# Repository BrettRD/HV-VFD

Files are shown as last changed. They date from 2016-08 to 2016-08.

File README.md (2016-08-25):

# HV-VFD
Staging point for design of a motor controller to suit electric vehicles.

This project is intended as a rework of https://github.com/vedderb/bldc-hardware/ to suit systems operating beyond the power ratings of the VESC 4.x.

## Major design goals:
* 400V tolerant system.
* 400A overcurrent survivability.
* FET desaturation detection.
* Maximise forward compatibility with existing development efforts.
* Traction power and logic level isolation
* Flexibility for alternate applications.

### FETs
This design will be based on the SEMiX402GB066HDs by Semikron, but will hopefully support everything in their SEMiX_2s pack.  
This sets the price point fairly high, but will require a rock solid gate driver design.  
I expect this project to branch for different IGBT sizes.  

### FET Drivers
The FET drivers need an estimated 6A to reach 400A IGBTs  
Currently designing around the 1EDI60H12AH by infineon

### Desaturation detector / phase shunt monitor
Depending on the required bandwidth for the phase shunts, a PWM based isolation amp like the IRF2277 might suffice.  
This design will also include a Vsat monitor on all fets, but probably just a fast comparator.  
Current best practice for IGBTs seems to be soft shutdown at some Vsat threshold, for MOSFETs Vsat only helps with estimating the total instantaneous heat power per junction.  

### Architecture
External logic lines will not be linked to traction power in any way.  
High voltage gate drivers are isolated by default, and are mostly available as single-gate drivers.  
Gate handling logic will be on the logic-side, so desat detect and shunt monitoring will all require isolation.  
Given the FET package and the current, the shunts will almost certainly be off-board which makes Hall effect sensors less of a design change.

## Considerations:
### Phase or Rail shunts:  
Phase shunt amplifiers need seperate power supplies and isolation gear, offset calibration is less trivial.  
Phase shunts measure both incoming and outgoing current. KCL should apply to the motor but when it doesn't, you want to know. This also allows automatic gain calibration.  
VESC5 looks like using phase shunts. Using isolation amps, this design could be left configurable. or I could include both.

### Crazy shit not yet dismissed:
* FPGA gate handling logic (iCE40 with yosys)  
  This allows us to do interesting things to the gate drive signals like configurable dead-time/overlap, spike quenching, fast ADCs and thermal modelling of FET junctions.
  Upgrading to the STM32F405VG (100pin pack) offers a 16b wide 80MHz DMA bus.
* ADCs on traction side of isolation barrier.  
  Saves on isolation amplifiers and noise.  
  The STM32F4 has a really nice ADC architecture with custom triggers, DMA, and 12b 6MS/s over 24 channels.

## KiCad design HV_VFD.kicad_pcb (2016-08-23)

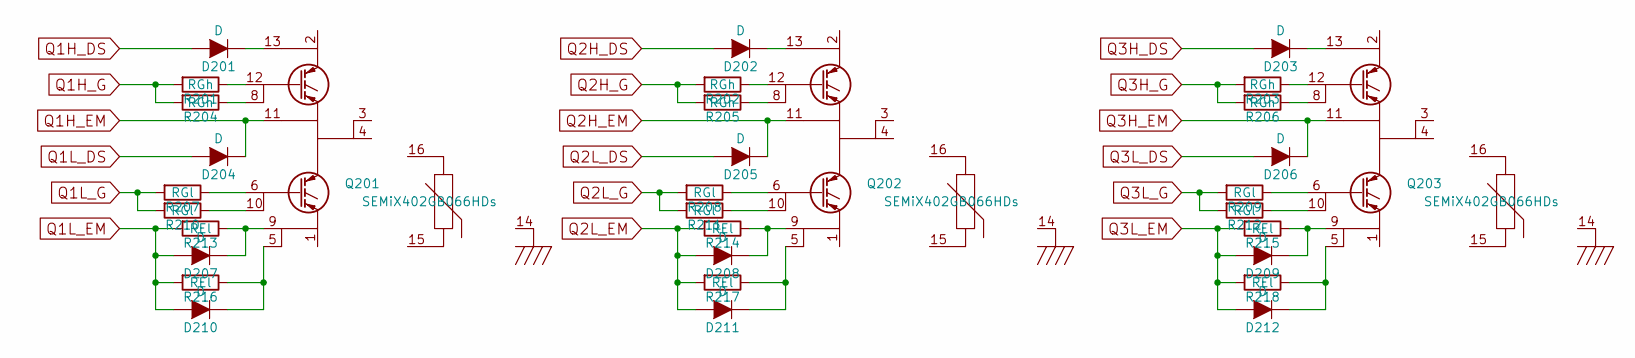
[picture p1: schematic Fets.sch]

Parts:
D201, D202, D203, D204, D205, D206: D; MELF_Standard
D207, D208, D209, D210, D211, D212: D; DO-214AB
Q201, Q202, Q203: SEMiX402GB066HDs; SEMiX_2s_7nc
R201, R202, R203, R204, R205, R206: RGh; R_1812
R207, R208, R209, R210, R211, R212: RGl; R_1812
R213, R214, R215, R216, R217, R218: REl; R_1812

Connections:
unnamed: D201.1 (K), Q201.13
unnamed: D202.1 (K), Q202.13
unnamed: D203.1 (K), Q203.13
unnamed: D207.1 (K), Q201.9, R213.1
unnamed: D208.1 (K), Q202.9, R214.1
unnamed: D209.1 (K), Q203.9, R215.1
unnamed: D210.1 (K), Q201.5, R216.1
unnamed: D211.1 (K), Q202.5, R217.1
unnamed: D212.1 (K), Q203.5, R218.1
unnamed: Q201.6, R207.1
unnamed: Q201.8, R204.1
unnamed: Q201.10, R210.1
unnamed: Q201.12, R201.1
unnamed: Q202.6, R208.1
unnamed: Q202.8, R205.1
unnamed: Q202.10, R211.1
unnamed: Q202.12, R202.1
unnamed: Q203.6, R209.1
unnamed: Q203.8, R206.1
unnamed: Q203.10, R212.1
unnamed: Q203.12, R203.1
Q1H_DS: D201.2 (A); also elsewhere on the board
Q1H_EM: D204.1 (K), Q201.11; also elsewhere on the board
Q1H_G: R201.2, R204.2; also elsewhere on the board
Q1L_DS: D204.2 (A); also elsewhere on the board
Q1L_G: R207.2, R210.2; also elsewhere on the board
Q2H_DS: D202.2 (A); also elsewhere on the board
Q2H_EM: D205.1 (K), Q202.11; also elsewhere on the board
Q2H_G: R202.2, R205.2; also elsewhere on the board
Q2L_DS: D205.2 (A); also elsewhere on the board
Q2L_G: R208.2, R211.2; also elsewhere on the board
Q3H_DS: D203.2 (A); also elsewhere on the board
Q3H_EM: D206.1 (K), Q203.11; also elsewhere on the board
Q3H_G: R203.2, R206.2; also elsewhere on the board
Q3L_DS: D206.2 (A); also elsewhere on the board
Q3L_G: R209.2, R212.2; also elsewhere on the board

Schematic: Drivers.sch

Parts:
C301, C302, C303, C304, C305, C306: C; C_1206
D301, D302, D303: D; MELF_Standard
R301, R302, R303, R310, R311, R312: R; R_0603
R304, R305, R306, R307, R308, R309: R; R_1812
U301, U302, U303, U304, U305, U306: 1EDI60H12AH; PG-DSO-8-59

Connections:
+15V: C301.1, C303.1, C305.1, D301.2 (A), D302.2 (A), D303.2 (A), R310.2, R311.2, R312.2, U304.6, U305.6, U306.6
GNDD: U301.3, U301.4, U302.4, U303.4, U304.4, U305.4, U306.4
unnamed: R304.2, U301.7
unnamed: R305.2, U302.7
unnamed: R306.2, U303.7
unnamed: R307.2, U304.7
unnamed: R308.2, U305.7
unnamed: R309.2, U306.7
unnamed: U301.2, U304.3
Q1H_BS: C302.1, D301.1 (K), R301.2, U301.6
Q1H_DS: R301.1; also elsewhere on the board
Q1H_EM: C302.2, U301.5; also elsewhere on the board
Q1H_G: R304.1, U301.8; also elsewhere on the board
Q1L_DS: R310.1; also elsewhere on the board
Q1L_G: R307.1, U304.8; also elsewhere on the board
Q2H_BS: C304.1, D302.1 (K), R302.2, U302.6
Q2H_DS: R302.1; also elsewhere on the board
Q2H_EM: C304.2, U302.5; also elsewhere on the board
Q2H_G: R305.1, U302.8; also elsewhere on the board
Q2L_DS: R311.1; also elsewhere on the board
Q2L_G: R308.1, U305.8; also elsewhere on the board
Q3H_BS: C306.1, D303.1 (K), R303.2, U303.6
Q3H_DS: R303.1; also elsewhere on the board
Q3H_EM: C306.2, U303.5; also elsewhere on the board
Q3H_G: R306.1, U303.8; also elsewhere on the board
Q3L_DS: R312.1; also elsewhere on the board
Q3L_G: R309.1, U306.8; also elsewhere on the board
VCC: U301.1, U302.1, U303.1, U304.1, U305.1, U306.1

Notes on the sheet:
Qxx_DS is the IGBT collector voltage clamped at the bootstrap rail voltage. -Used for Desaturation detection.
QxH_BS is the Bootstrap rail voltage of the high side drivers -This rail may need trickle charging.
The Eice Driver has a neat inverting pin behaviour Shown here wired to prohibit shoot-through Not the final gate logic.

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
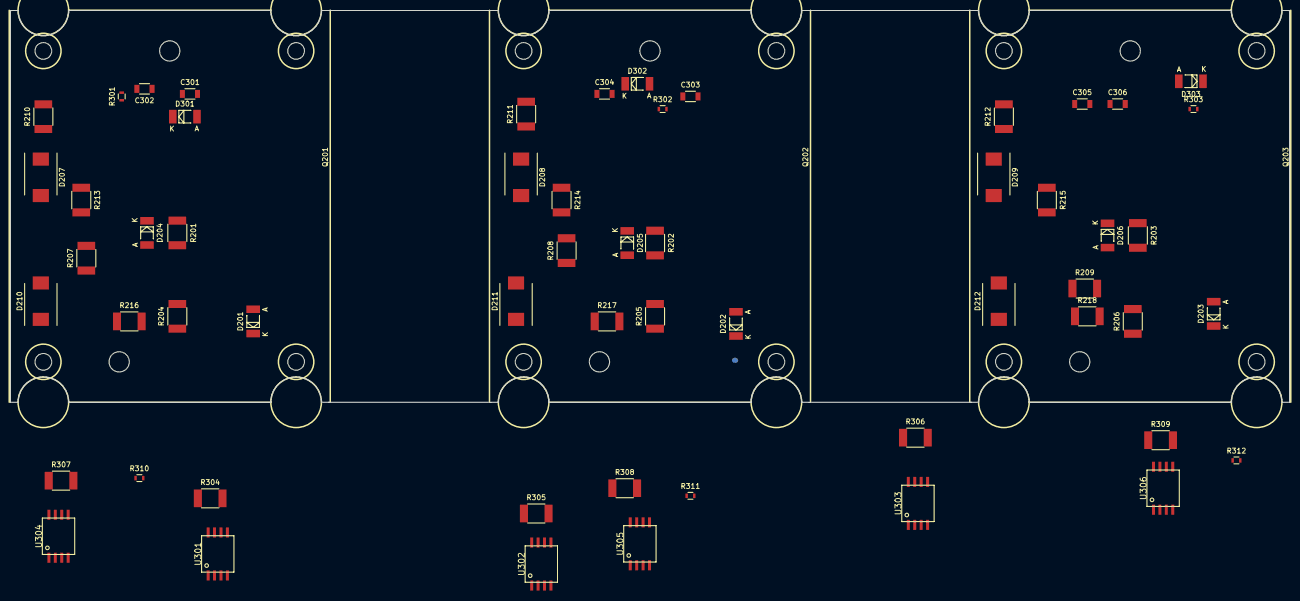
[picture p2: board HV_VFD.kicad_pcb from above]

Board: 2 copper layers, 253.0 x 77.5 mm, 60 parts (0 on the bottom side), 51 nets.

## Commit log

2016-06-22 added footprint and PCB sizing experiments
    [HV_VFD.kicad_pcb, HV_VFD.sch]
2016-06-22 added basic bootstrap and desat diodes
    [Drivers.sch, Fets.sch, HV_VFD.kicad_pcb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]
2016-06-22 Added FET choice, updated target architecture.
2016-08-23 added gate drivers, increased FET spacing
    [Drivers.sch, Fets.sch, HV_VFD.kicad_pcb]
